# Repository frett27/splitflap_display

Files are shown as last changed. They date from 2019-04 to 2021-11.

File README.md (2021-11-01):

# Split Flap Display

*Patrice Freydiere - Avril/Septembre 2019*

This repository contains the technical elements to create a flip flap display module, This display can be used for a physical web counter, a clock, letter display.

Parametric design permit to use other elements to display (picto, drawing).

### Key Design Concept

The FlipFlap module aim to reduce the number of part to build it. Modules are connected to each others and contribute to display large messages. The module is only responsible to manage the mechanics and contribution intelligence.

Using standard PVC card helps have nice diplay digits, they are easy to setup as there are printers allowing to create the fonts.

Using SCAD as modeler permit to have adaptative design, and change the dimensions.

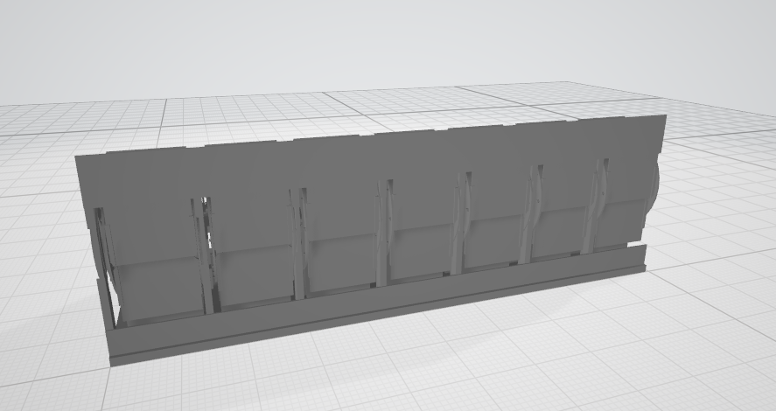
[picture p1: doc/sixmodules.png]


Four Spaces Modules:

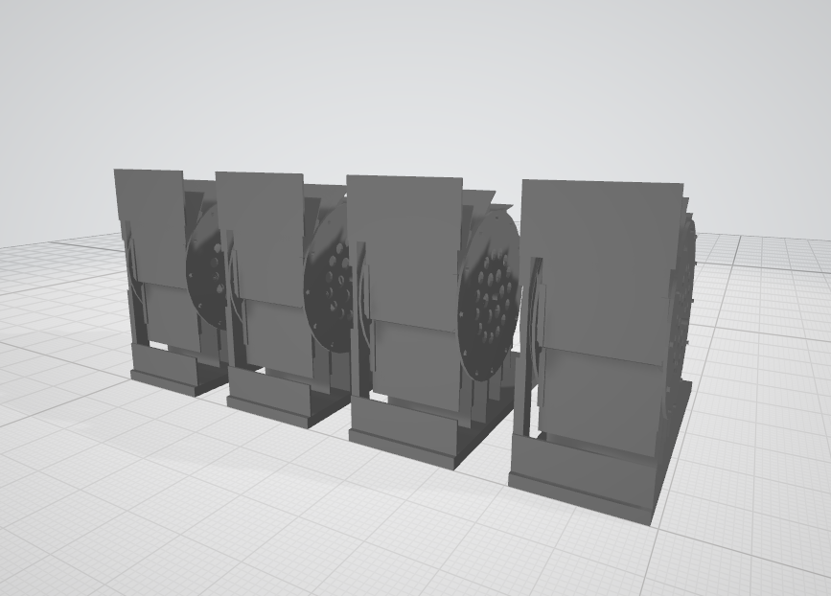
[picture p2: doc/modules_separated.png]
 

Exploded view of one module : (4 main printed parts + cards)

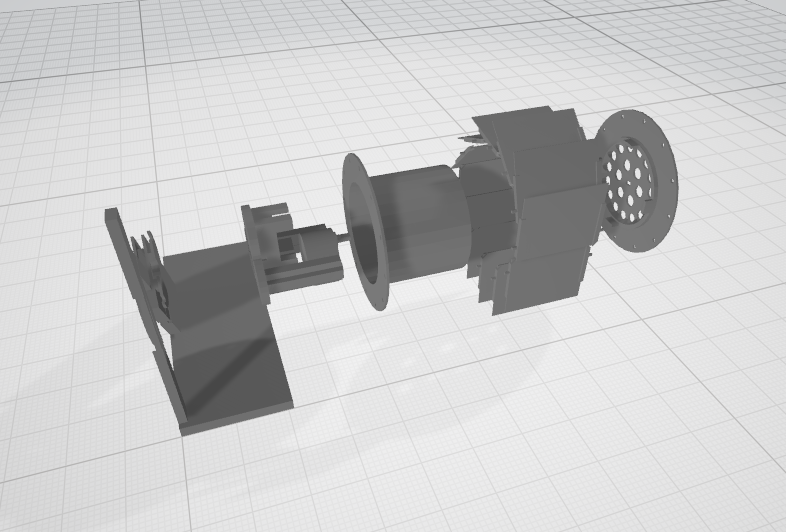
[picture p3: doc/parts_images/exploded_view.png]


This project is used for side projects. All comments, improvements are welcome.

The 3D design aim to be printed, with a minimum parts number. 

for more informations, go to **doc/** folder on how to print and build

# Project State

#### V1

- [x] 3D Print - V1 
- [x] Electronic Schematic
- [x] Card Mounting
- [x] Software
- [x] Structure for fix

#### V2

3D Design

- [x] Thick enlrge for switch
- [x] Redesign card fixtures
- [x] Support Design, to be simple light and permit to add decorations.
- [x] Add switch on electronic Card & Pullup

#### **V2.1**

- [x] Testing the Software Serial, apparently an error in choosing the pins 3 is not interrupted changed compatible ->, use 8 or 9

#### **V3 - New electronic**

integrating the upstream serial and downstream serial, works both.

#### **V4 - Electronic change**

Fix a pin placement issue

## Credits

This project is inspired from  [Dead_simple_split_flap_display_ 's work](https://www.thingiverse.com/thing:2369832)

And [splitflap](https://github.com/scottbez1/splitflap) work (upon the buiding simplification)

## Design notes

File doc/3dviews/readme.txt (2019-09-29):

Stl Viewer v1.07
================

Installation:
-------------
upload those files into your web server:
stl_viewer.min.js 
parser.min.js 
load_stl.min.js 
webgl_detector.js 
CanvasRenderer.js 
OrbitControls.js
TrackballControls.js
Projector.js 
three.min.js

Usage:
------
At the html body:

<script src="stl_viewer.min.js"></script>

<script>
	var stl_viewer=new StlViewer(document.getElementById("stl_cont"), { models: [ {id:0, filename:"mystl.stl"} ] });
</script>

Documentation & License details:
--------------------------------
https://www.viewstl.com/plugin/

by Omri Rips, Viewstl.com

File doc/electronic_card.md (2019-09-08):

# Electronic Card

*Patrice Freydiere - 2019*

The electronic is module specific, but can be connected with others modules to create a variable length number.

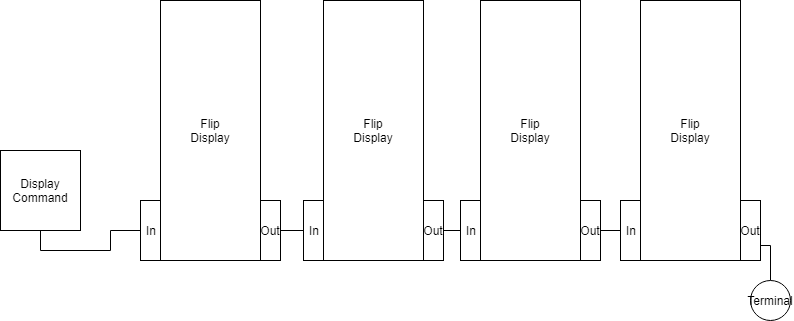
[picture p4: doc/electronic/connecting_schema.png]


Every modules have a in-connector and out-connector. They transmit information upward and backward using a serial communication.

Inside the module, the main controller, is connected to the stepper motor driver, and the out-connector.

Basic schema of the electronic elements associated to modules :

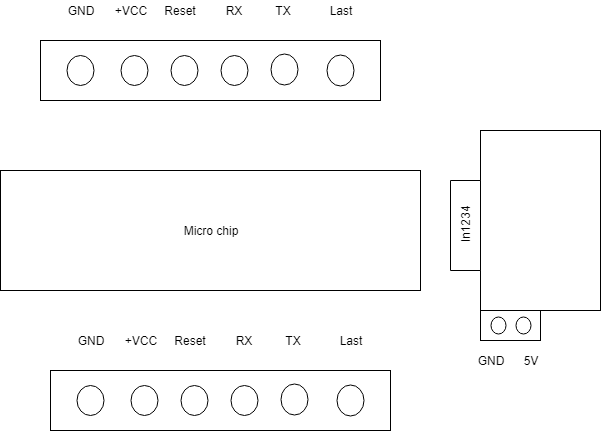
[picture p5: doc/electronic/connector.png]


## Electronic Schema

The schema is as follow :

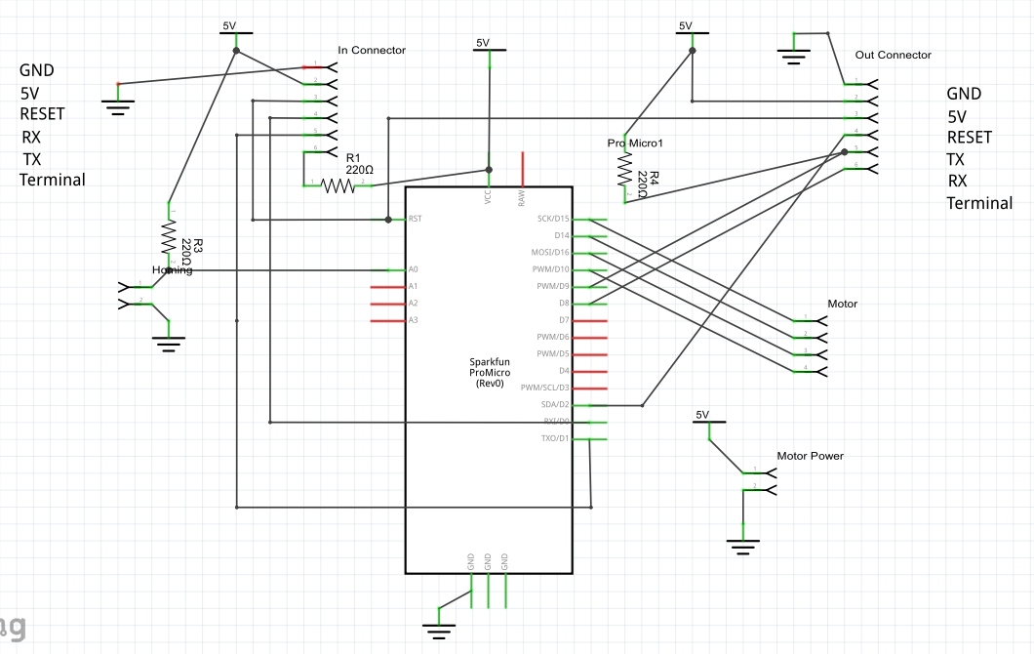
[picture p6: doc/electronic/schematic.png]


### Connector pins

Slot from the input side

<-  on the input side

- GND
- VCC
- RESET
- RX
- TX
- pull up connection

On the other side / symetric

- GND
- VCC
- RESET
- TX
- RX
- Connected

### The electronic software logic:

To have more information about the control of the digit using the serial port, see [](flip_controlling.md)

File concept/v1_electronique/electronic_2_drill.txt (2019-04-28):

; NON-PLATED HOLES START AT T1
; THROUGH (PLATED) HOLES START AT T100
M48
INCH
T1C0.086614
T100C0.035000
T101C0.035433
T102C0.038000
%
T1
X018699Y001581
X001735Y001722
X001524Y012808
X018875Y012914
T100
X010034Y004460
X017034Y010460
X016034Y010460
X014034Y010460
X018034Y004460
X013034Y010460
X008320Y013113
X007034Y010460
X015034Y004460
X010034Y010460
X009034Y004460
X012034Y004460
X008034Y004460
X004320Y013113
X011034Y004460
X018034Y010460
X015034Y010460
X009034Y010460
X017034Y004460
X012034Y010460
X008034Y010460
X016034Y004460
X011034Y010460
X014034Y004460
X013034Y004460
X007034Y004460
T101
X014760Y009341
X019560Y006221
X016680Y008861
X012360Y006221
T102
X014414Y001602
X002343Y010150
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

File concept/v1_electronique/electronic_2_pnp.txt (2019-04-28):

*Pick And Place List
*Company=
*Author=
*eMail=
*
*Project=electronic_2
*Date=22:58:21
*CreatedBy=Fritzing 0.9.2b.11.19.8d2d5970658f0bed09c661c9ea9a515b5f40f44c
*
*
*Coordinates in mm, always center of component
*Origin 0/0=Lower left corner of PCB
*Rotation in degree (0-360, math. pos.)
*
*No;Value;Package;X;Y;Rotation;Side;Name
1;;;37.1785;-30.0187;90;Bottom;TXT3
2;;;9.1479;-25.4851;0;Bottom;TXT3
3;;THT;35.9448;-32.1225;90;Bottom;In Connector
4;;;28.7267;-1.64689;90;Bottom;TXT3
5;;;42.2378;-30.0701;90;Bottom;TXT3
6;;;29.3816;-30.2896;90;Bottom;TXT3
7;;;12.6508;-3.29659;0;Bottom;TXT1
8;;;31.3944;-15.8039;0;Bottom;Via3
9;;;39.7373;-30.2059;90;Bottom;TXT3
10;;;15.7577;-5.1997;0;Bottom;TXT1
11;;THT;5.95336;-24.5128;0;Bottom;Motor
12;;;4.40904;-4.37463;0;Bottom;Hole2
13;;;34.467;-30.3414;90;Bottom;TXT3
14;;THT;5.417;-11.4922;0;Bottom;Motor Power
15;;;47.4965;-4.01706;0;Bottom;Hole1
16;;;3.87269;-32.5335;0;Bottom;Hole4
17;;;47.9435;-32.8016;0;Bottom;Hole3
18;;;7.90221;-13.1062;90;Bottom;TXT3
19;;;9.07006;-28.1321;0;Bottom;TXT3
20;;;49.6824;-15.8039;0;Bottom;Via2
21;;;33.1065;-18.9495;90;Bottom;Pro Micro1
22;;;42.3672;-22.5095;0;Bottom;Via1
23;;;36.5236;-1.37596;90;Bottom;TXT3
24;220;THT;16.053;-33.3083;-180;Bottom;R1
25;;;9.30361;-20.191;0;Bottom;TXT3
26;;;37.4904;-23.7287;0;Bottom;Via4
27;;;7.98007;-9.99205;90;Bottom;TXT3
28;;;41.5829;-1.42741;90;Bottom;TXT3
29;;;31.3608;-1.69869;90;Bottom;TXT3
30;;;39.0824;-1.56322;90;Bottom;TXT3
31;;THT;35.3421;-4.06946;90;Bottom;Out Connector
32;;;34.1153;-1.56322;90;Bottom;TXT3
33;;;9.18683;-22.877;0;Bottom;TXT3
34;;;32.0609;-30.464;90;Bottom;TXT3

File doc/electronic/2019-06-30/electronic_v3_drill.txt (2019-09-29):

; NON-PLATED HOLES START AT T1
; THROUGH (PLATED) HOLES START AT T100
M48
INCH
T1C0.086614
T100C0.035000
T101C0.035433
T102C0.038000
%
T1
X018685Y017217
X001461Y017174
X001672Y001500
X018541Y001486
T100
X017910Y012301
X014910Y012301
X013910Y012301
X008910Y012301
X016910Y006301
X011910Y012301
X010060Y014917
X007910Y012301
X015910Y006301
X006060Y014917
X010910Y012301
X009910Y006301
X012910Y006301
X010181Y010503
X006910Y006301
X016910Y012301
X015910Y012301
X009910Y012301
X017910Y006301
X017126Y008793
X012910Y012301
X006910Y012301
X014910Y006301
X013910Y006301
X013126Y008793
X008910Y006301
X006181Y010503
X011910Y006301
X007910Y006301
X010910Y006301
T101
X006840Y017485
X007080Y016285
T102
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

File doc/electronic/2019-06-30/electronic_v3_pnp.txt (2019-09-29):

*Pick And Place List
*Company=
*Author=
*eMail=
*
*Project=electronic_v3
*Date=16:30:38
*CreatedBy=Fritzing 0.9.2b.11.19.8d2d5970658f0bed09c661c9ea9a515b5f40f44c
*
*
*Coordinates in mm, always center of component
*Origin 0/0=Lower left corner of PCB
*Rotation in degree (0-360, math. pos.)
*
*No;Value;Package;X;Y;Rotation;Side;Name
1;;;36.363;-2.74234;90;Bottom;TXT3
2;220;THT;20.7815;-26.6781;0;Bottom;R4
3;;THT;35.7038;-42.731;90;Bottom;In Connector
4;;THT;35.2619;-5.83768;90;Bottom;Out Connector
5;;;31.2002;-3.06507;90;Bottom;TXT3
6;;;8.02289;-33.0397;0;Bottom;TXT3
7;;;8.06181;-30.4316;0;Bottom;TXT3
8;;;31.8199;-41.0725;90;Bottom;TXT3
9;;;17.9832;-41.3643;0;Bottom;Via2
10;;;41.4223;-2.79379;90;Bottom;TXT3
11;;;47.0948;-3.77611;0;Bottom;Hole1
12;;;41.9968;-40.6787;90;Bottom;TXT3
13;;;34.226;-40.9499;90;Bottom;TXT3
14;;THT;11.3984;-42.7993;90;Bottom;Homing
15;;;25.7204;-10.8755;0;Bottom;TXT1
16;;;17.3736;-44.4123;0;Bottom;Via1
17;;;3.71208;-43.6241;0;Bottom;Hole4
18;;;33.9547;-2.92961;90;Bottom;TXT3
19;;THT;3.80977;-12.2156;0;Bottom;Motor Power
20;;;28.5661;-3.01327;90;Bottom;TXT3
21;;;29.1406;-40.8981;90;Bottom;TXT3
22;;;47.4614;-43.7316;0;Bottom;Hole3
23;;;7.49799;-14.8946;90;Bottom;TXT3
24;220;THT;38.4222;-22.3355;180;Bottom;R3
25;;;36.9375;-40.6272;90;Bottom;TXT3
26;;;4.24845;-3.81223;0;Bottom;Hole2
27;;;39.4963;-40.8145;90;Bottom;TXT3
28;;;32.7933;-23.6268;90;Bottom;Pro Micro1
29;;;38.9218;-2.92961;90;Bottom;TXT3
30;;;8.17859;-27.7456;0;Bottom;TXT3
31;;;7.42012;-18.0088;90;Bottom;TXT3
32;;;14.5797;-1.36796;0;Bottom;TXT1
33;;;7.94503;-35.6868;0;Bottom;TXT3
34;;THT;3.94431;-31.8263;0;Bottom;Motor
35;220;THT;20.4732;-37.8894;180;Bottom;R1

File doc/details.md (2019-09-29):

# A more detailed insight about Split flap display module

The FlipFlap module aim to reduce the number of part to build it.  4 printed parts are needed to build one. 



a PCB manage motors and serial communication on both usage : standalone, or serial.

Modules does not include the front panel. this permit to change color, boxing.



Four Modules:

 

Exploded view of one module : (4 main printed parts + cards)

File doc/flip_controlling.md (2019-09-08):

# Flip controlling - Protocol

*Patrice Freydiere - 2019*

### Introduction

This document describe the flip display protocol. It implements a minimum protocol, with an integrated message control, using the length.

The module has two Serial Port for communication : In and Out. And one serial port for command.

Digits module elect the master at the top left of the chain, every digits modules are connected in a serial manner.

### Message protocol

To remain simple, easy to analyze and DEBUG, all messages are in text format.

All Internal messages are sent using the following envelope structure :

"S" + [SIZE_3DIGITS] + [MSG] + [10]

if the message has 10 characters, it is escaped using the "\\" character. 

## Chain control

At init, the module wants to know if he is the latest one, to determine it's number in the stack.

Protocol to initialize the module: send IAM-[] message, the message will be serially forwarded with an updated address. This permit the chain to allocate their addressID. 

By default the initialized id is -1 for each module

| Sequence | Message | Message Orientation | Description | Note |
| --- | --- | --- | --- | ---- |
| 2 | IAM-[NoATTRIBUTED] | [->] MODULE [->] | Define the address for the module. The message is forwarded to the next one, with the next NoAttributed. | |
| 4 | CMD-[NoAttributed]-[MessageLength]-[Command] | [->] MODULE | This command permit to send a specific message to a digit module | |
| 1 | DISPLAY-[MESSAGE] | [->] MODULE [->] | Ask to display the message, the module take the [No] digit number. Each Digits are on 2 digits | |
| 2 | ACKDISPLAY-[NoAttributed] | [<-] MODULE | Acknowledge about the message | |

## Module Display Command

| ID | Message | Message Orientation | Description | Note |
| ---- | --- | --- | --- | --- |
| 3 | DIGIT-[DIGITNO] | [->] MODULE | Ask to display the given digit | Display the digit  number (from 0-12). no ack for this operation |
| 4 | OFFSET | [->] MODULE | Define the homing offset to tune the position of the first flip | |

## Module Stepper Command (Testing)

| ID | Message | Message Orientation | Description | Note |
| ---- | --- | --- | --- | ---- |
| 1 | MOVE-[step] | [->] MODULE | move the digit module to the given step | |

## Module HeartBeat

| ID | Message | Message Orientation | Description | Note |
| ---- | --- | --- | --- | ---- |
| 1 | HELLO | [->] MODULE [->] | Preceding module inform of its status, following module responde HELLO Message also | |

## Error Handling

In case states are not properly covered, some error messages can be sent.

| ID | Message | Message Orientation | Description | Note |
| ---- | --- | --- | --- | ---- |
| 1 | ERROR-[MESSAGE] | [<-] MODULE [<-] | inform of an error | |

## Debug Message

In debugging status, messages can be send, they are not handled by up and down

| ID | Message | Message Orientation | Description | Note |
| ---- | --- | --- | --- | ---- |
| 1 | DEBUG-[MESSAGE] | [->] MODULE [<-] | debug message sent | |

## Message examples

**Hello Message**

```
S005HELLO
```

Response on command Port:

```
Command from Front Executed :HELLO
front send message:S005HELLO
```

**Print a specific DIGIT**

```
S008DIGIT-02
```

Response on command port

```
Command from Front Executed :DIGIT-02
```

**Move stepper to a specific step**

```
S008MOVE-003
```

Response:

```
Command from Front Executed :MOVE-500
```

**Define the offset of the stepper initial offset**

```
S011OFFSET-0500
```

response:

```

Command from Front Executed :OFFSET-0500

```

## Chain Command Examples

to initiate the hole chain, you have to call the IAM function that define the addresses of all connected modules

**Define the chain addresses of modules**

```
S005IAM-0
```

```
Command from Front Executed :IAM-0
back send message:S005IAM-1
```

**Send a specific command to a module in the chain**

```
S016CMD-001-DIGIT-08
```

```
Command from Front Executed :CMD-001-DIGIT-08
Command from Front Executed :DIGIT-08
1750 / 4096
```

**Send a hole display message to the chain**

```
S013DISPLAY-06234
```

Response

```
command from Front Executed :DISPLAY-06234
front send message:S012ACKDISPLAY-1
```

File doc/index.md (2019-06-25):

# Flip Flap - Digit - module (FLIP-1)

*Patrice Freydiere - 2019-04*

This module display a digit, using an energy minimum approach. 



## Feature

- Affordable

- easy to create and mount
- Adaptative

## Dimensions

The module has the following dimensions currently, using a PVC card as reference for the digits.

 "depth=", 109.55, "width=", 59.98, "height=", 152.2

## Components

| Reference | Qty  | Description | Cost Home Made (€) | Cost Parts |
| --- | ---- | --- | --- | --- |
| FLIP-1-3D1 | 1 | Stator | 2 | 5€ / per 20 parts  |
| FLIP-1-3D2 | 1 | Rotor - 1 | 2 | 5€ / per 20 parts  |
| FLIP-1-3D3 | 1 | Rotor - 2 | 2 | 5€ / per 20 parts  |
| FLIP-1-3D4 | 1 | Support for sustain the display | 3 | 10€ / per 20 parts |
| FLIP-1-CARDS | 6 | Flip cards (6 * 2) half cards | 30€ per 500 pieces | |
| FLIP-1-MOTOR_CMD | 1 | 28byj-48 - module with command card (LN218) | 4 € each | |
| FLIP-1-SWITCH | 1 | Homing switch | 2 € each | |

<u>Currently in tests:</u>

Vinyl letters :

<https://www.amazon.com/dp/B079HJRG1X/ref=sspa_dk_detail_0?pd_rd_i=B077KDX4NR&th=1>

(2inch)

## 3D model

Model is build with OpenScad, permitting to create parametric models, this is really usefull for optimization and alternatives.

There are 4 parts, 



The support :

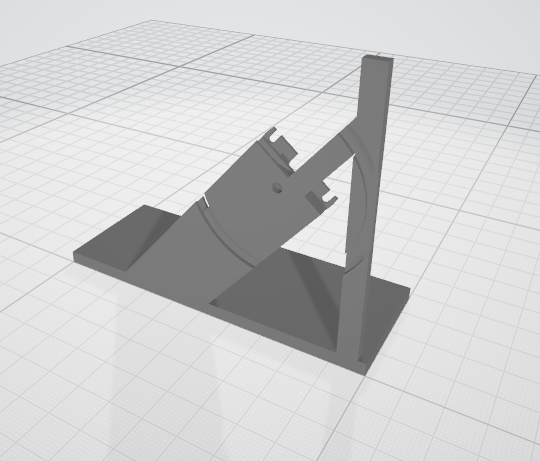
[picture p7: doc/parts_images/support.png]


The rotor in 2 parts, 

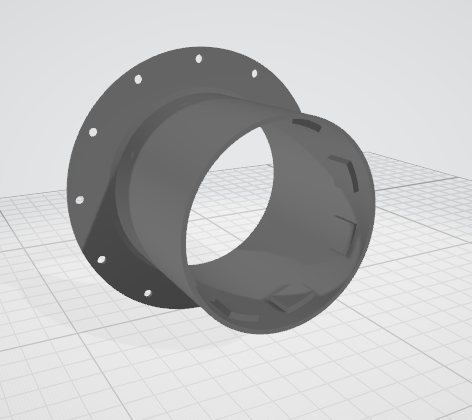
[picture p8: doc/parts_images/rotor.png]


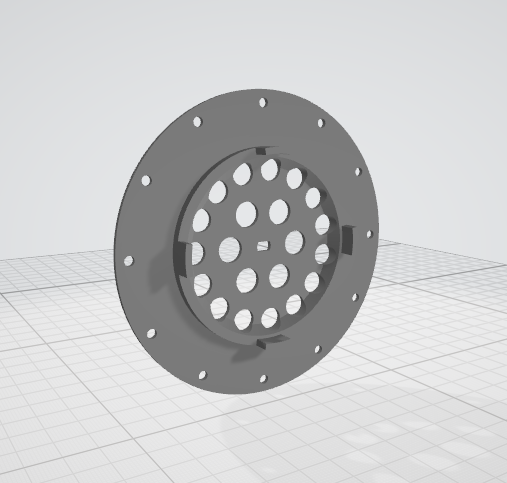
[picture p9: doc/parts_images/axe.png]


And the stator for the mounting elements :

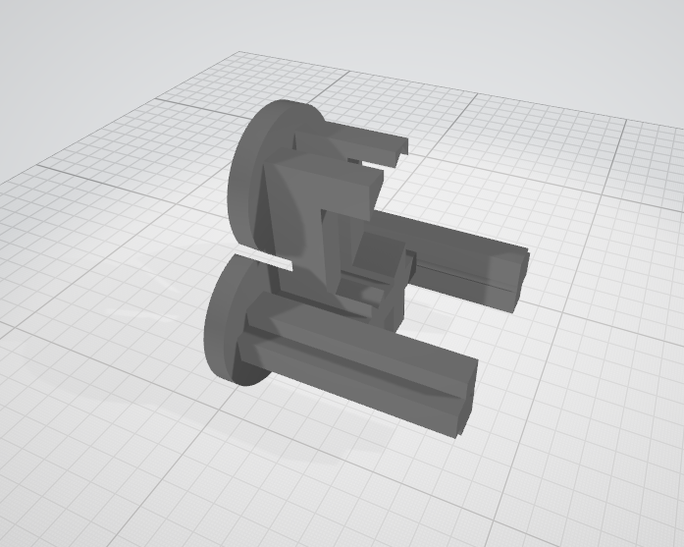
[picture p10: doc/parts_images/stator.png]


And for card fix :

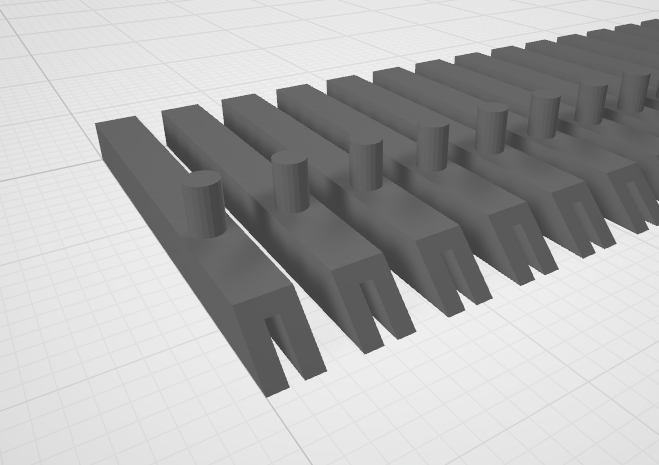
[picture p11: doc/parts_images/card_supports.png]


## Electronic

Electronic card is composed of a leonardo microchip, this chip handle the motor, homing, and communication. And external USB connected unit gives the numbers to display.

A lonely electronic card is hosted in the display.

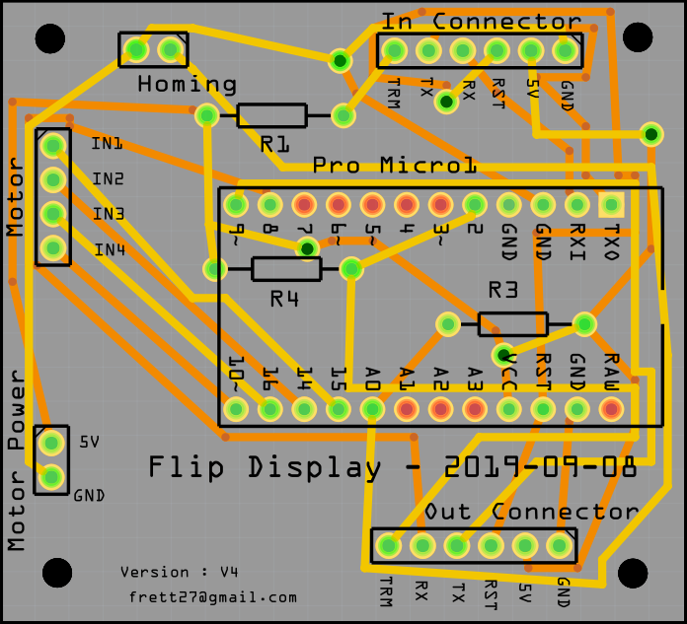
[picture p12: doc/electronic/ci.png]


## How to mount flip display

Step 1 : solder the switch, 

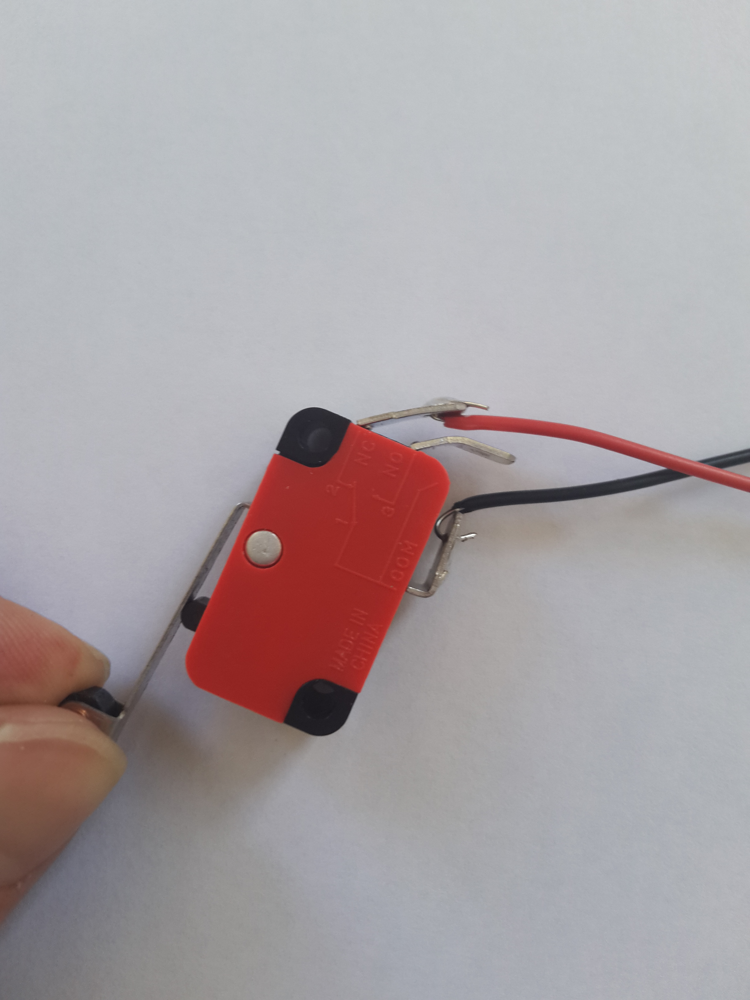
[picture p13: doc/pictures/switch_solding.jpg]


Mount motor on stator :

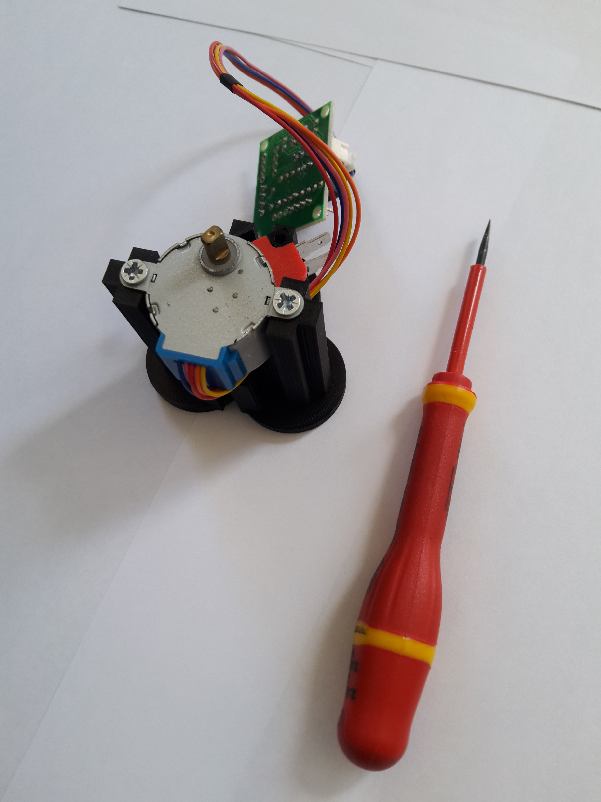
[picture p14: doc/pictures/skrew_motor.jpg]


Switch soldering

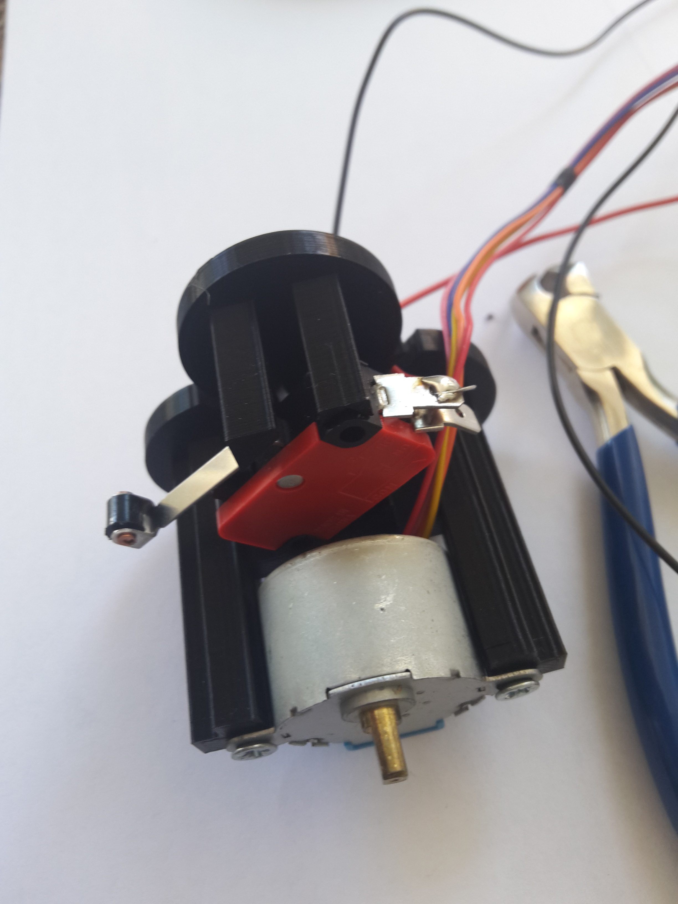
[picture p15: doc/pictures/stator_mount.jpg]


Put the stator into the mounted rotor and fix them on the support using the 2 skrews. Take caution of the cable there is calculated space to not make the cable be damaged.

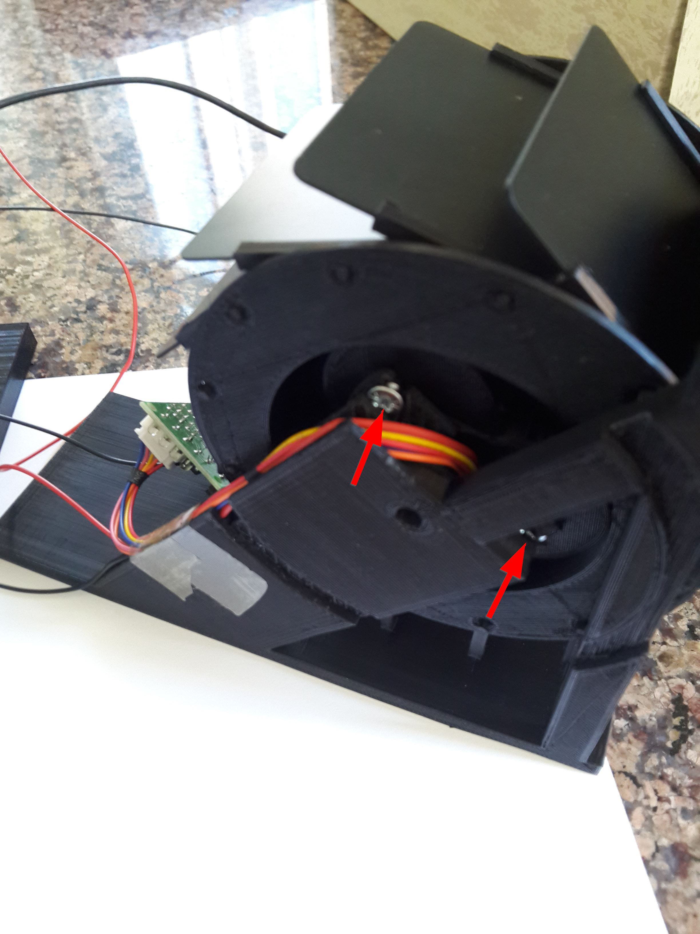
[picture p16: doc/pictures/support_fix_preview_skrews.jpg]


The mounted result :

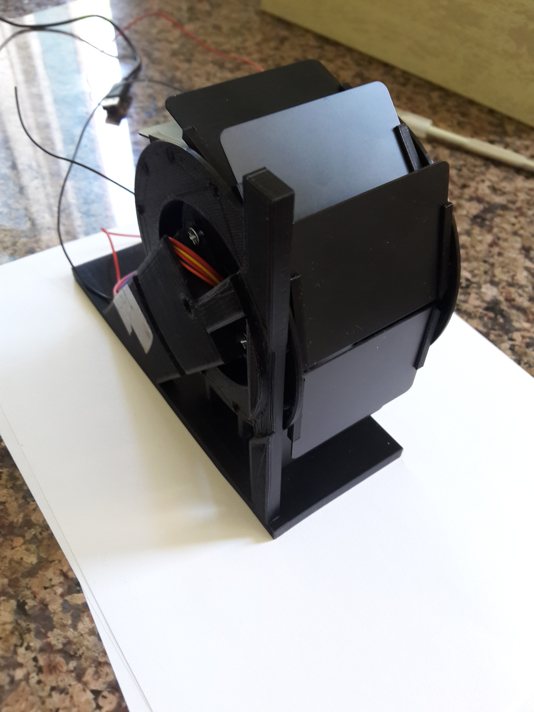
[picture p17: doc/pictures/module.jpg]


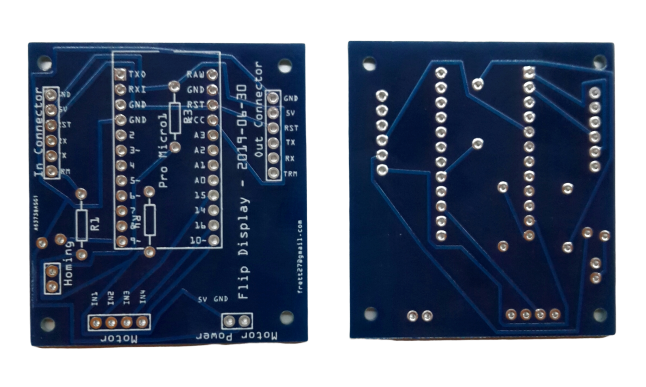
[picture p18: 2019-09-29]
doc/electronic/cards_v3-nobg.png

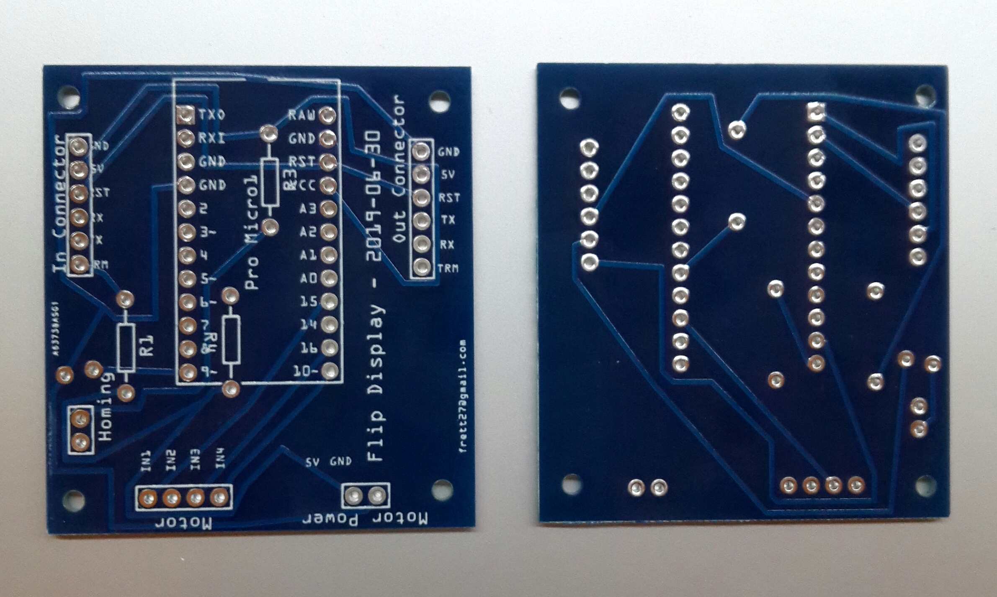
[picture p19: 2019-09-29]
doc/electronic/cards_v3.jpg

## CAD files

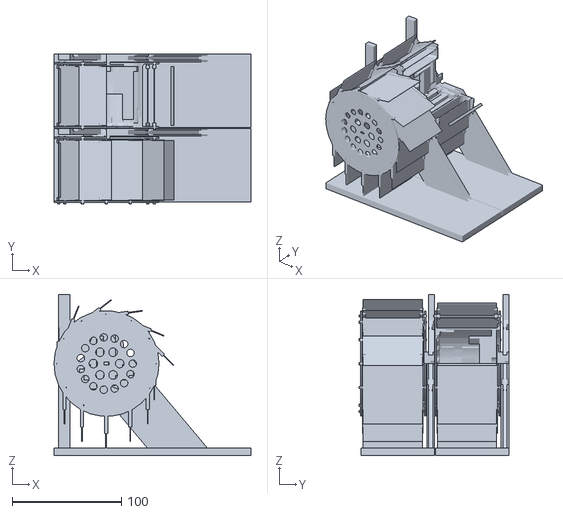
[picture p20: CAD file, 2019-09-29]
doc/3dviews/view_2_modules_with_cut.stl
180.0 x 136.8 x 147.3

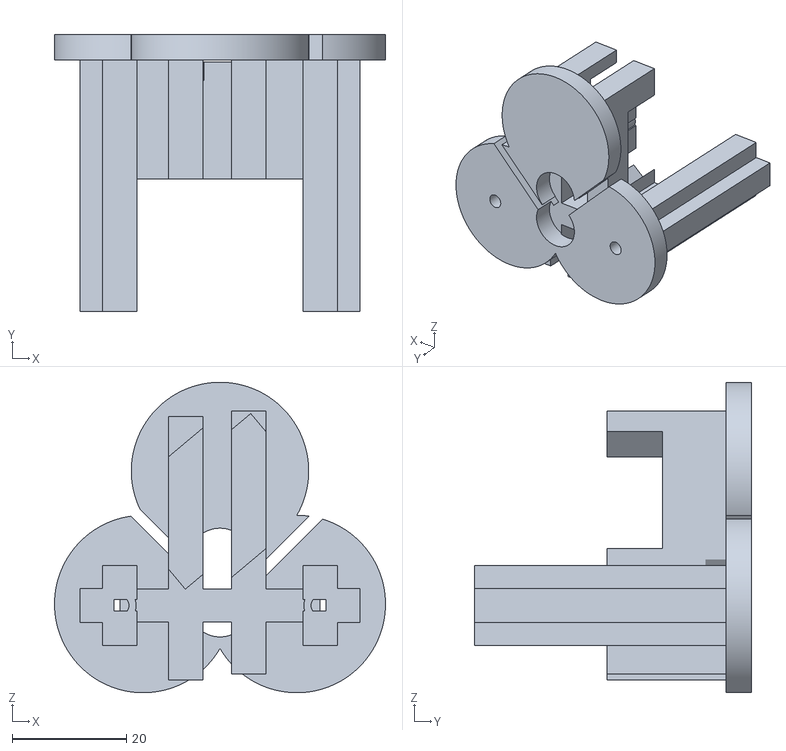
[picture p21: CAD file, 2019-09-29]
stl/stator.stl
57.8 x 48.5 x 54.3

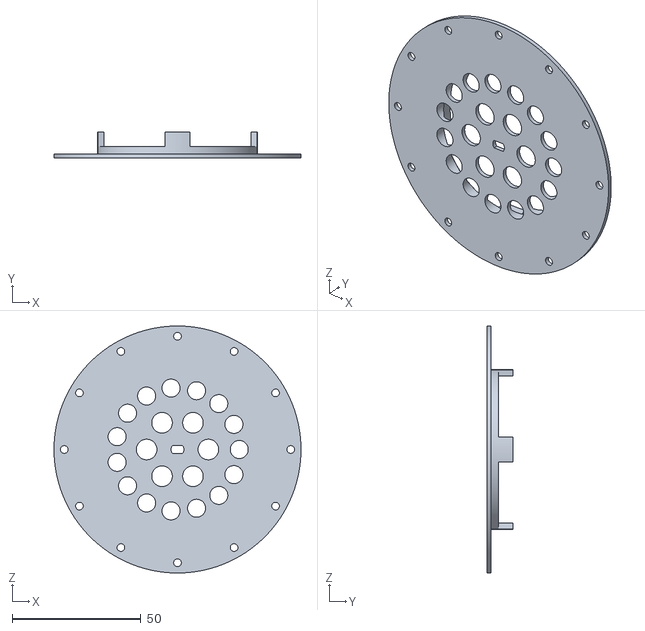
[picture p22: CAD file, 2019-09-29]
stl/axe.stl
96.0 x 10.0 x 96.0

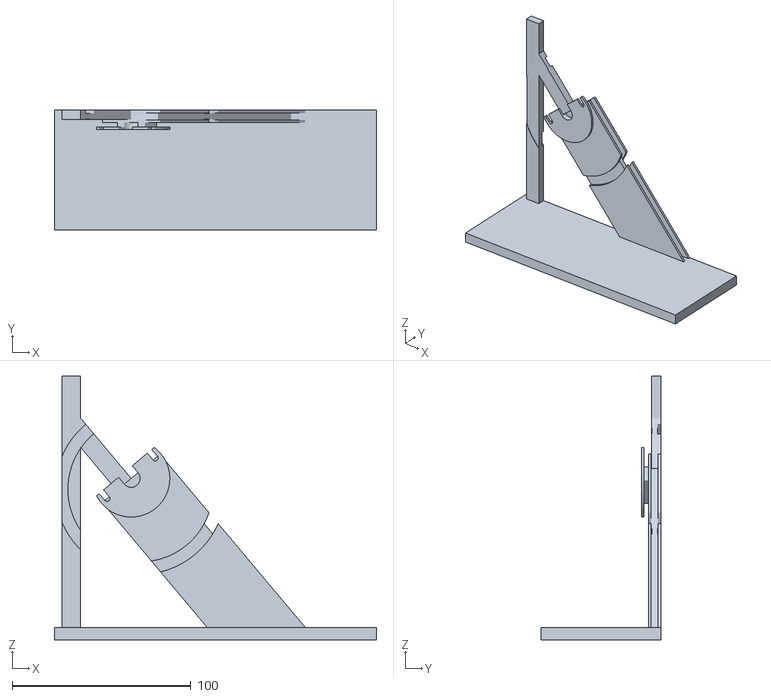
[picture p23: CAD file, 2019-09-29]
stl/support.stl
180.0 x 67.0 x 147.3

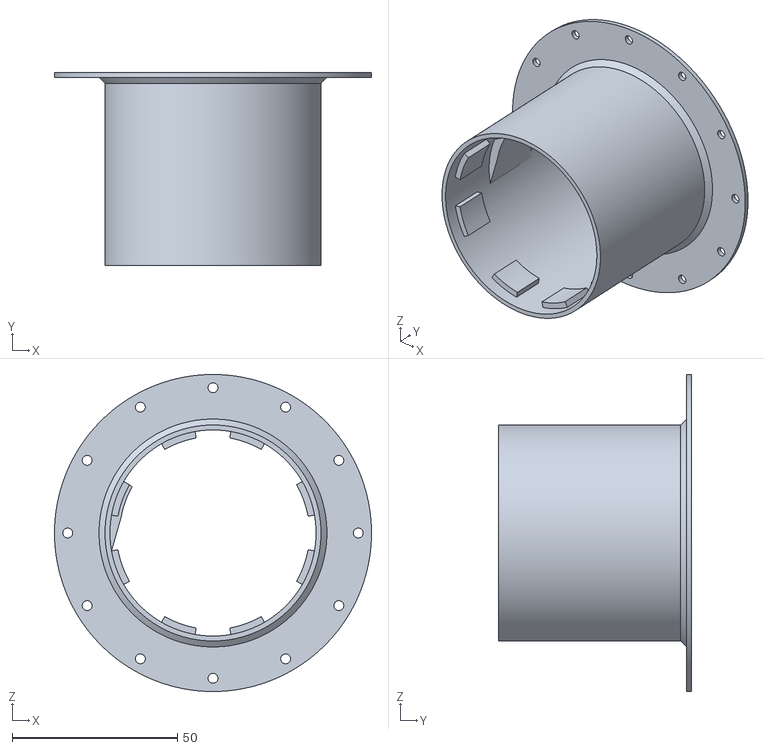
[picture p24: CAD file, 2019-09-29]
stl/rotor.stl
96.0 x 58.4 x 96.0

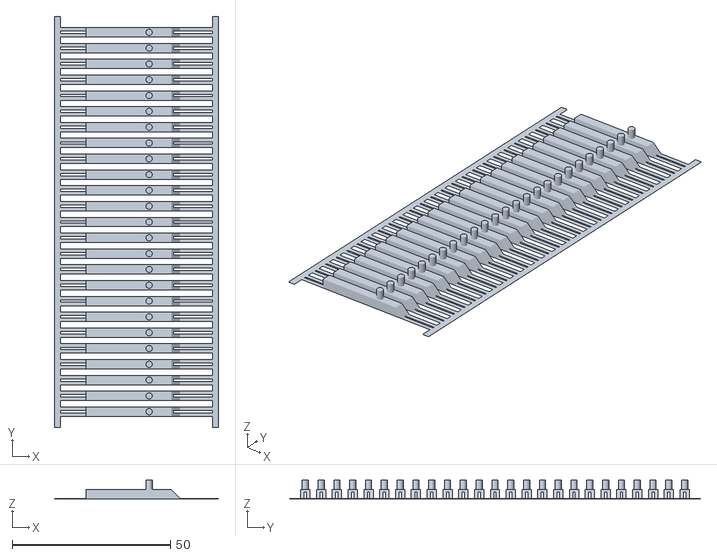
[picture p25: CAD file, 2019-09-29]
stl/fixations.stl
52.0 x 130.0 x 6.00

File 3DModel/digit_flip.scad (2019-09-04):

include <relativity.scad>
include <28byj-48.scad>
include <switch.scad>

////////////////////////////////////////////////////////////
//
//  Parameters for the design
//
////////////////////////////////////////////////////////////

// pvc card dimensions

pvc_card_width = 53.98;

// card support thick
support_flip_thick = 0.75;

flip_width = pvc_card_width + 2*support_flip_thick;
flip_height = 86.2/2; //2
flip_thick = 0.75;

flips_numbers = 12;
thick = 1.5;

// fixture size
flip_fixure_diameter = 2;

// play for the flip fixture, for rotating
flip_fixure_diameter_play = 1; // in diameter

// radius for flip rotating fix

/* initialement 42 */
radius_flip_position = 44; 
// flip axis distance
/* initialement 7.5 */
deport = 10;

// distance between the flip holes and external
margin_axe_external = 4;

// motor distance link
max_internal_radius = 42 /* radius_flip_position */ - 11;

// play for letting the elements move
// 0.2 is good
play = 0.2;
transverse_play = play + 0.5;


/////////////////////////////////
// internal generation parameters

angle_flip = 360/flips_numbers;
axe_external_diameter = 
                (radius_flip_position +
                 margin_axe_external) * 2;

// internal centring
internal_centring_elements_height = 2;

fixing_height = 28byj48_chassis_height + (flip_width - 28byj48_chassis_height) - 28byj48_shaft_height + 28byj48_shaft_slotted_height / 2;

// general animation angle parameters
general_rotation_angle = 0;

// drawing generation precision
// uncomment this for generating STL,
//

 $fa = 1;
 $fs=0.3;


module flip(width=flip_width) {
    // flip_fixure_diameter/2
    translate([0,0,0]) {
        
        translate([0,deport,0]) { // deport
            box(size=[width - 2 * support_flip_thick,
                        flip_height,
                        flip_thick],
                anchor=[0,1,1]);
        }


        // 1 
        translate([-width/2+support_flip_thick,0,0])
        rotate([0,180,0]) // flip to have the pin on proper direction
       
        rotate([0,0,90]) // orient along card
        translate([0,0, flip_thick / 2])
        support_flip_card_reference();
        
        translate([width/2 - support_flip_thick,0,0])
        
        rotate([0,0,90]) // orient along card
        translate([0,0, - flip_thick / 2])
        support_flip_card_reference();
                
    }
}


module axe() {
    
     rotate([0,general_rotation_angle,0]) {
            translated(thick/2 * y)
            orient([y])
            differed("hole")
            
            rod(d=axe_external_diameter ,h=thick)
            
            for (i = [0: flips_numbers]) {
                orient([z])
                rotated(angle_flip*i*z)
                translated(radius_flip_position  *x)
                rod(d=flip_fixure_diameter 
                       + flip_fixure_diameter_play,h=10, $class="hole");
            }
        };
}

module axe_with_holes() {
  
    difference() {
       
        union(){
            
          rotate([-90,0,0])
          rotate_extrude(convexity = 10)
          polygon(points = [
            [ (max_internal_radius) ,
               0],
            [  (max_internal_radius) ,
               3 * thick],
            [  (max_internal_radius - 2 * thick) ,
               3 * thick],
            
            [(max_internal_radius - 5 * thick) ,
               0]
          ]);
          axe();
            
          // pattes   
          
          for(i = [0:3]) {
              internal_radius = max_internal_radius;
              element_width = 10;
            
              rotated([0,90 * i,0])
              translate([0,element_width/2,-internal_radius])
              rotate([90,0,0])
              arc(rayon=internal_radius,
                  height=internal_centring_elements_height,
                  width=element_width, 
                  angle_start=-9, 
                  angle_end=9);

          }
            
          // axis tube
          
          rotate([90,0,0])
          translate([0,0,-thick])
          cylinder(d = 28byj48_shaft_radius * 3, h = thick);
            
        };
        
        // holes
        union() {
            
                // internal
                nb_internal = 6;
                for( i = [0:nb_internal]) {
                    rotate([0,i * 360/nb_internal +
                    general_rotation_angle,0])                    translate([12,10*thick,0]) 
                    rotate([90,0,0]) 
                    cylinder(d=8,h=20*thick);
                };
            
                for( i = [0:15]) {
                    rotate([0,i * 360/15 +
                        general_rotation_angle,0])                    translate([24,10*thick,0])
                    rotate([90,0,0])
                    cylinder(d=7,h=20*thick);
                };
        }
    }
    
   
    

}

// function to place flips with angle and index
module place_flip(index = 0, relative_angle = 0) {
     // second flip
    rotate([0, - index * angle_flip + general_rotation_angle ,0]) {
        translate([radius_flip_position,flip_width/2,0]) {
            rotate([0,
                    -90 + relative_angle 
                        - general_rotation_angle,
                    0]) {
                rotate([0,0,90]) {
           
                flip(width= flip_width);
             }
            }
        }
    }
}


// place the flips around the 12 holes design
module montage() {
    
    // one flip
    
    place_flip(0, relative_angle = 180);
    place_flip(1, relative_angle=180 - 15);
    place_flip(2, relative_angle=180 - 8);
    place_flip(3, relative_angle=180 - 8);
    place_flip(4, relative_angle=180 - 8);
    place_flip(5, relative_angle=180 - 8);
    place_flip(6, relative_angle=180 - 0);
    place_flip(7, relative_angle=angle_flip);
    
    place_flip(8, relative_angle=2 * angle_flip);
   
    place_flip(9, relative_angle=3 * angle_flip);

    place_flip(10, relative_angle=4 * angle_flip);

    place_flip(11, relative_angle=5 * angle_flip);
   
}

/*
// place the butee for the flip
module butee() {
    butee_width = flip_width + 2 * thick;
    translated( (flip_width * z) + 
            ( radius_flip_position + thick) * x - 
            2 * thick * z 
               )
    box(size = [2,butee_width,5],anchor=[-1,-1,-1]);
}
*/

// show motor
module motor() {
    differed("bords") {
        
        rod(d = 20, h = 25,anchor=[0,0,1])
        align([0,0,1]) {
            rod(d = 2, h=8.1);
        
            translated((20/2 + 15.1/2) * x + -30 * z) 
            box(size=[20, 30, 30], $class="bords");

            rotated(180*z)
            translated((20/2 + 15.1/2) * x + -30 * z) 
            box(size=[20, 30, 30], $class="bords");
        }
    };
}

// utility tube module
module tube(d,h,perfo) {
    differed("trou","plein") {
     rod(d=d, h=h, $class="plein",anchor= [0,0,-1] );
     translate( [0,0,-1]) rod(d=perfo,h=h+2, anchor= [0,0,-1] , $class="trou");
 }
}


module threecircles(diameter=20, flips_numbers=5, height=thick) {
    
    rod(d=diameter, h=height);
    for(i = [0:360/flips_numbers:360]) {
        rotated([0,0,i])
        translated(diameter/2 * x)
        rod(d=diameter, h=height);    
    }
}

skrew_hole_size = 28byj48_mount_hole_radius * 2-1;
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

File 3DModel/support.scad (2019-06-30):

// use <libraries/paratslot_for_openscad_201205/paratslot.scad>

include <digit_flip.scad>;


// distance from axis to base
structure_height = (flip_height - deport + radius_flip_position);

// echo (structure_height);

bottom_support_height = 7;

sustain_structure_thick = 7;


angle_pylon = 40;

height_axis = 2*28byj48_shaft_offset;

main_structure_height = (structure_height * 2)/cos(angle_pylon);


diameter_flip= 2 * radius_flip_position;




//$fa = 1;
//$fs=0.3;


////////////////////////////////////////////////////
//

module _support_pylon_real() {
    translate([-2 * sustain_structure_thick,0,0])
    for (i = [0:2]) {
        translate([i*14,0,0])
        translate([0,3.5,-main_structure_height/2])
        twotslot(h=structure_height,w=sustain_structure_thick);
    }
}

module _support_pylon() {
    
    pylon_width = 42;
    
    difference() { // for hole for the next axis
        
        union() {
            difference() {
               box(size=[pylon_width,sustain_structure_thick,      
                         main_structure_height],
                         anchor=[0,-1,1]);
            
               // cable pass
               depth = 6;
               mirror([1,0,0])
               union() {
                   // on the pylon side
                   translate([-pylon_width/2,
                                thick])
                   box(size= [depth, sustain_structure_thick - 2 * thick, 
                              main_structure_height],
                        anchor=[-1,-1,1]);
                   
                   // on the top to help guide the cables
                   rotate([0,-angle_pylon/2,0])// angle for passing cables
                   translate([0,thick,0])
                   box(size= [pylon_width, 
                          sustain_structure_thick - 2 * thick,
                          depth],
                        anchor=[0,-1,-1]);
                   
                   
               }
            }
            
            // upper support
            upper_pylon_width = sustain_structure_thick * 3 / 4;
            translate([0,
                       sustain_structure_thick - upper_pylon_width]) {
                d = pylon_width/4;
                
                
                    box(size=[d,
                              upper_pylon_width,
                              radius_flip_position ],
                        anchor=[1,-1,-1]);
                
                translate([0,0, radius_flip_position])
                rotate([0,angle_pylon,0])
                box(size=[d,
                          upper_pylon_width,
                          (flip_height - deport)*sin(45)], // angle
                    anchor=[1,-1,-1]);
                    
                translate([0,0, radius_flip_position])
                rotate([0,angle_pylon,0])
                box(size=[d,
                          upper_pylon_width,
                          main_structure_height],
                    anchor=[1,-1,1]);
                
            }
        }
        
            // hole for passing the next module axis
         hole_diameter = 28byj48_shaft_radius * 2 + play;
         translated(- 28byj48_shaft_offset*z 
                    + (sustain_structure_thick ) *y) 
                // for having the hole at 0
         orient(y)
         rod(d=hole_diameter, 
             h=sustain_structure_thick , 
             anchor=[0,0,0]);
    }
}

// _support_pylon();

top_distance = radius_flip_position + (flip_height - deport)*sin(45);
distance_to_support = 4; // mm from holes


// distance_to_support = 6; // mm from holes

module oblong(width=10, height=30, thick=2, class="oblong") {
    rod(d=width,h=thick, $class=class)
    box(size=[width,height,thick],anchor=[0,1,0], $class=class);
}


module _support_fixation_stator() {
        orient([0,1,0])
        differed("hole") {
                
                rod(h=thick, 
                d= 2 * 28byj48_mount_center_offset 
                    + skrew_hole_size +5 ,
                anchor =[0,0,-1])
                align([0,0,1])
                translated(5*y)
                box(size=[20,
                          10,
                          distance_to_support - thick],
                    anchor=[0,0,-1])
               
                 
                translated(-10*y)
                box(size=[50,50,50],$class="hole", 
                            anchor=[0,1,0]);
            
                // central    
                oblong(thick=90, 
                       width=10, 
                       class="hole");
                
                // trous        
                translated((height_axis + skrew_hole_size / 2)*x)
                oblong(width=skrew_hole_size,thick=90 , class="hole");
                translated(-(height_axis + skrew_hole_size /2)*x)
                
                
                oblong(width=skrew_hole_size,thick=90 , class="hole");
                
                
        }

}
// offset_part = 55;

// distance from center motor axis and the fixing
// plane
offset_part = 56.5;


module ground() {
    translated(- (structure_height + bottom_support_height) * z)
    box(size=[500,500,500],anchor=[0,0,1]);
}

module support() {
    rotated( -angle_pylon *y)
    translated(offset_part * y) {
        
        difference() {    
            translated(28byj48_shaft_offset*z)
            {
                _support_fixation_stator();
                
                translated(distance_to_support*y)
                
                _support_pylon();

                
            };
            
            // pin way
            union() {
                margin = 7;
                way_height = 2;
                
                // 1st way
                translated(distance_to_support*y - 0.01 * y)
                rotate([-90,0,0])
                tube(d=diameter_flip + margin,
                       perfo=diameter_flip - margin,
                       h=way_height);
                
                // 2nd way
                translated( (distance_to_support 
                             + sustain_structure_thick 
                            - way_height) * y)
                rotate([-90,0,0])
                tube(d=diameter_flip + margin,
                       perfo=diameter_flip - margin,
                       h=way_height + 0.1);
                
            }
        }
    }
    
    dalle_g();
}

// support();

base_support_width = 180;

module front_panels() {
    
     // bottom
     translated((offset_part 
                + distance_to_support 
                + sustain_structure_thick) * y
                -structure_height *z +
    
               -(base_support_width / 2 
                    - axe_external_diameter / 2 + thick) * x
               )
     box(size = [thick,base_support_large, 20 ], 
         anchor=[1,1,-1] );

     // up
     translated((offset_part 
                + distance_to_support 
                + sustain_structure_thick) * y
                + top_distance *z +
    
               -(base_support_width / 2 
                    - axe_external_diameter / 2 + thick) * x
               )
     box(size = [thick,base_support_large, 35 ], 
         anchor=[1,1,1] );


}

// support();

//front_panels();

base_support_large = 60 + sustain_structure_thick;

module dalle_g() {
   
    translated((offset_part 
                + distance_to_support 
                + sustain_structure_thick) * y
                -structure_height *z +
               (base_support_width / 2 - axe_external_diameter / 2) * x
               )
   dalle(); 
    
}

module dalle() {
    // dalle
    
    box(size=[base_support_width, base_support_large ,          bottom_support_height], 
        anchor=[0,1,1]);
    
}


///////////////////////////////////////////////////////////
// Assembly


module display_modules(number_of_modules = 6, margin = 2) {

    multiple_shift_position = base_support_large;
    for( i = [0:number_of_modules]) {
        
        translate([0, -(multiple_shift_position + margin) * i,0]) {
                
            difference() {
             support();
             ground();
            }
            
            axe_with_fix();
            montage_g();
            rotor_g();
            stator_g();
            front_panels();
            
        }
    }

}

/*
rotate([-90,0,0]) {
display_modules();
}
*/

module global_support() {
    difference() {
             support();
             ground();
            }
}


module cut_view() {

    difference() {
        
        display_modules(number_of_modules = 1, margin = 1);
        // cut to check
        translate([0,-10,0])
        cube(size=[1000,1000,1000]);
    }
}

/*
 // best view with stl viewer
rotate([-90,0,0])
cut_view();
*/


module exploded_view() {

    global_support()

    translate([0,-50,0])
    stator_motor_g();

    translate([0,-120,0])
    rotor_g();

    translate([0,-200,0])
    montage_g();
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

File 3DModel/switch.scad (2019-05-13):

include <relativity.scad>


inter_axes = 24.45;
switch_angle0 = atan(9.41/inter_axes);
switch_angle1 = atan(4.61/inter_axes);

switch_width = 28.2;
switch_height = 16;
switch_deep = 9.70;



module target(angle) {
    
    
}

// hole 1.5 du bord
switch_holes_size = 3;
switch_edge_distance = 1.3;

module switch_holes(d=switch_holes_size, h = 10) {
      // 3mm
        translate([ d/2 + switch_edge_distance,
                    d/2 + switch_edge_distance,
                    0])
        cylinder(d=d,h=h);
        
        translate([switch_width - (d/2 + switch_edge_distance), 
                  switch_height - (d/2 + switch_edge_distance),
                  0])
        cylinder(d=d,h=h);
    
}

module switch_body() {

    difference() {
        translate([ +switch_width/2,
                    switch_height/2,
                    switch_deep/2])
        switch_body_centered()
        //cube(size=[switch_width, switch_height, switch_deep]);
        switch_holes();
    }
}

module switch_body_centered() {
    box(size=[switch_width, switch_height, switch_deep]);
}

module switch(angle = switch_angle0, drawboth=0) {
    
    switch_body();

    // axe
    t_width = 0.6;
    t_large = 4.4;
    h_axe = 2.5;

    inter_axes = 24.45;
    /// boule en bout
    touch_diameter=4.77;
    touch_large = 4.4;

    if (drawboth == 1) {
            
        translate([-t_width/2 + switch_width/2,switch_height - h_axe,switch_deep/2])
        rotate([0,0,90 - switch_angle0])
        box([t_width,inter_axes,t_large], anchor=[0,-1,0])
        align([0,1,0])
        rod(d=touch_diameter, h=touch_large, anchor=[0,0,0]);


        translate([-t_width/2 + switch_width/2,switch_height - h_axe,switch_deep/2])
        rotate([0,0,90 - switch_angle1])
        box([t_width,inter_axes,t_large], anchor=[0,-1,0])
        align([0,1,0])
        rod(d=touch_diameter, h=touch_large, anchor=[0,0,0]);

            
        
        
    } else {
            
        translate([ -t_width/2 + switch_width/2,
                    switch_height - h_axe,
                    switch_deep/2])
        rotate([0,0,90 - angle])
        box([t_width,inter_axes,t_large], anchor=[0,-1,0])
        align([0,1,0])
        rod(d=touch_diameter, h=touch_large, anchor=[0,0,0]);
    }
}

// switch();

// place connexions 

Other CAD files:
doc/3dviews/view_2_modules_with_cut_r.stl
3DModel/28byj-48.scad
3DModel/old_fixtures.scad

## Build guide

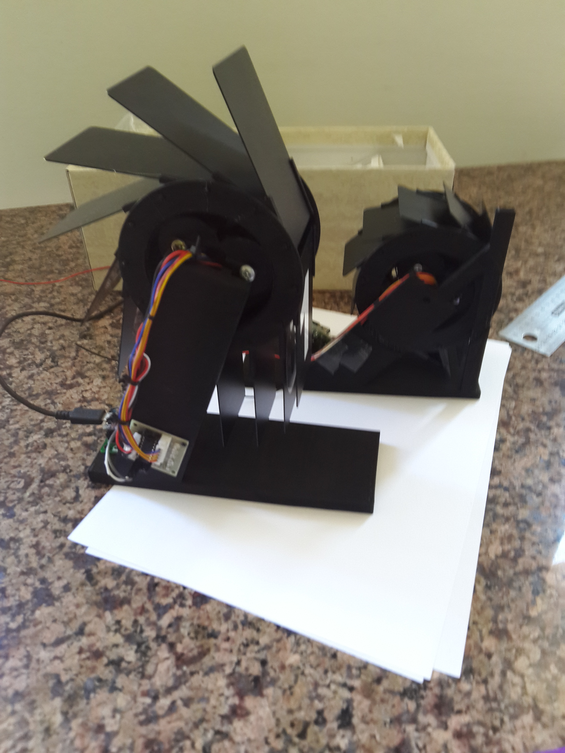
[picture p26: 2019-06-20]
doc/pictures/build/20190616_161145.jpg

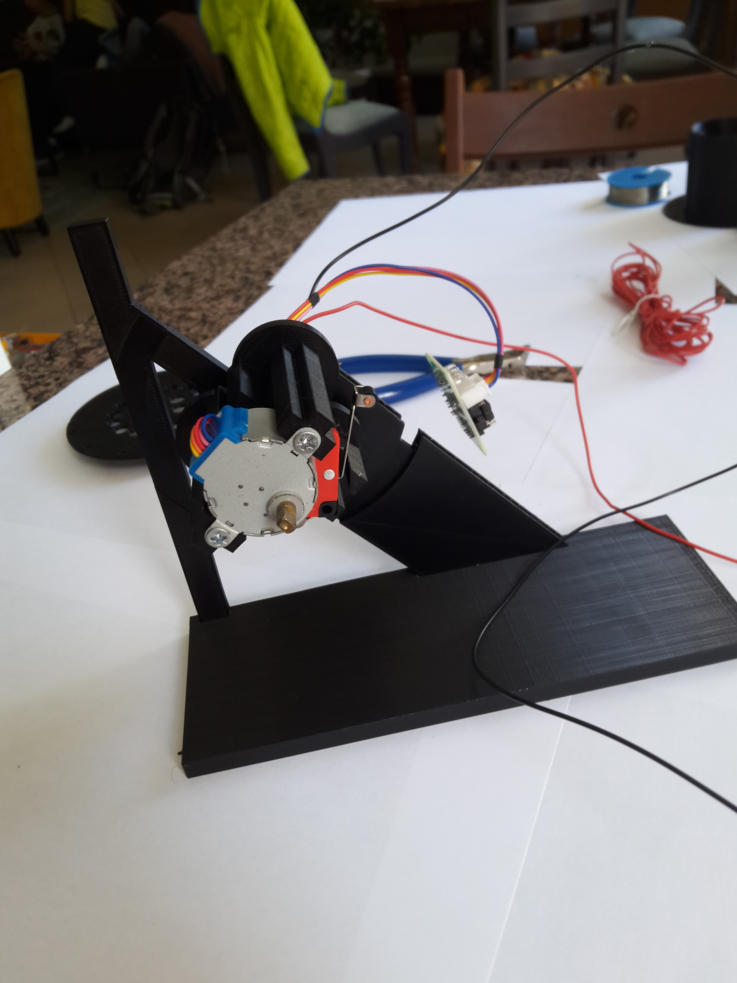
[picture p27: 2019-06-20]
doc/pictures/build/20190616_150015.jpg

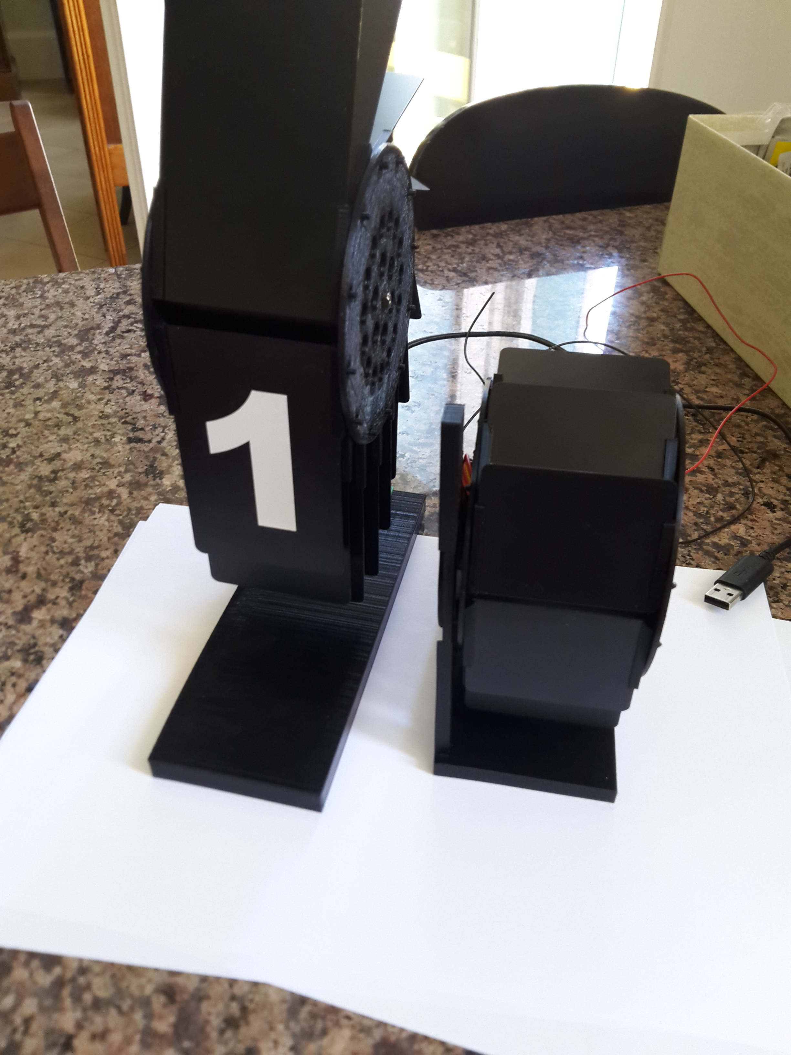
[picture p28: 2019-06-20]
doc/pictures/build/20190616_160147.jpg

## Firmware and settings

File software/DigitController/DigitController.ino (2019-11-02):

// Real Time Kernel
#include <Arduino_FreeRTOS.h>
#include "queue.h"

#include <EEPROM.h>

// Library for controling the stepper
#include "CheapStepper.h"

// manage the parsing of commands
#include "DigitCommandParser.h"

// Number of digits depends on the mecanical design
#define NUMBER_OF_DIGITS 12
#define MESSAGE_MAX_SIZE 30

// Time to wait on the message queue
#define MAXTOWAIT 100

#include <SoftwareSerial.h>



void TaskSerialProtocol(void *parameters);


/* Define the data type that will be queued. */
typedef struct A_Message
{
 char ucData[ MESSAGE_MAX_SIZE ];
} AMessage;

/* Define the queue parameters. */
#define QUEUE_LENGTH 2
#define QUEUE_ITEM_SIZE sizeof( AMessage )


static QueueHandle_t xFrontSendingQueue;
static QueueHandle_t xBackSendingQueue;

// attributed address of the module
static uint8_t attributedAddress = -1;


// global positionning (motor)
static int currentStep = -1;

// total step = -1 -> no homing done yet
static int totalSteps = -1;

// programmable offset
static int offsetStep = 0;

#define EEPROM_OFFSET_STORAGE_ADDRESS 0
#define EEPROM_OFFSET_STORAGE_MAGIX_HEADER 0xCC


  /*
  PIN D8 -> RX
  PIN D9 -> TX
  */
SoftwareSerial ds(8, 9); // RX, TX

int readOffsetValue() {
  byte v1 = EEPROM.read(EEPROM_OFFSET_STORAGE_ADDRESS);
  if (v1 != EEPROM_OFFSET_STORAGE_MAGIX_HEADER) {
    // no magic at start, no value read
    return 0; 
  }

  byte b1 = EEPROM.read(EEPROM_OFFSET_STORAGE_ADDRESS + 1);
  byte b2 = EEPROM.read(EEPROM_OFFSET_STORAGE_ADDRESS + 2);
 
  return b1 + (b2 << 8) - 2^15;
}

void writeOffsetValue(int valueToWrite) {
  uint16_t v = valueToWrite + 2^15;
  byte b1 = v & 0xFF;
  byte b2 = (v >> 8) & 0xFF;
  EEPROM.write(EEPROM_OFFSET_STORAGE_ADDRESS, EEPROM_OFFSET_STORAGE_MAGIX_HEADER);
  EEPROM.write(EEPROM_OFFSET_STORAGE_ADDRESS + 1, b1);
  EEPROM.write(EEPROM_OFFSET_STORAGE_ADDRESS + 2, b2);
}



void setup() {

  offsetStep = readOffsetValue();
  
  // initialize serial communication at 115200 bits per second for main serial
  Serial.begin(115200);
  Serial.print(offsetStep);

  // init back and front serial to 9600 bauds
  Serial1.begin(9600);
  ds.begin(9600);
  
 // while (!Serial) {
    ; // wait for serial port to connect. Needed for native USB, on LEONARDO, MICRO, YUN, and other 32u4 based boards.
 // }
  
   // Create the queue, storing the returned handle in the xQueue variable. 
  xFrontSendingQueue = xQueueCreate( QUEUE_LENGTH, QUEUE_ITEM_SIZE );
  if( xFrontSendingQueue == NULL )
  {
      // The queue could not be created. 
      Serial.println("Front Queue cannot be created");
  }

  // Create the queue, storing the returned handle in the xQueue variable. 
  xBackSendingQueue = xQueueCreate( QUEUE_LENGTH, QUEUE_ITEM_SIZE );
  if( xBackSendingQueue == NULL )
  {
      // The queue could not be created.
      Serial.println("Back Queue cannot be created");
  }

   
    // Now set up two tasks to run independently.
  xTaskCreate(
    TaskMotor
    ,  (const portCHAR *)"Motor Report"   // A name just for humans
    ,  128  // This stack size can be checked & adjusted by reading the Stack Highwater
    ,  NULL
    ,  2  // Priority, with 3 (configMAX_PRIORITIES - 1) being the highest, and 0 being the lowest.
    ,  NULL );

    
  // Now set up two tasks to run independently.
  xTaskCreate(
    TaskSerialProtocol
    ,  (const portCHAR *)"Serial"   // A name just for humans
    ,  300  // This stack size can be checked & adjusted by reading the Stack Highwater
    ,  NULL
    ,  2  // Priority, with 3 (configMAX_PRIORITIES - 1) being the highest, and 0 being the lowest.
    ,  NULL  );

  initMotor();
  
 
  vTaskStartScheduler();
}



static int objectifStep = -1; // no objectives


// Protocol handling
//    0 - Wait for Assigned Number
//    1 - Wait for Commands
//    

boolean startsWith(char *str, char *pattern) {
  unsigned int i = 0;
  for (;;) {
    if (str[i] == 0) {
      if (pattern[i] == 0) {
        // end of both
        return true;
      }
      // end of string
      return false;
    }
    if (pattern[i] == 0) {
      // end of pattern
      return true; 
    }
    if (str[i] != pattern[i]) {
      return false;
    }
    i++;
  }
}


void commandCanceled() {
  Serial.println("commandCanceled");
}

int readUpStream() {
  return Serial1.read();
}

int readUpStream2() {
  return Serial.read();
}


int readDownStream() {
  return ds.read();
}


static AMessage bufferMessage;
void pushMessageToQueue(char* message,QueueHandle_t queue) {

  int message_length = strlen(message);
  // copy message
  sprintf(bufferMessage.ucData, "S%03d%s\n", message_length, message);
  if (xQueueSend(queue, &bufferMessage, MAXTOWAIT) != pdPASS) {
    // issue in posting the element on the queue
    Serial.println(F("error in pushing the message"));
  }  
}

void moveTo(uint16_t digit) {
  uint16_t stepsInterval = totalSteps / NUMBER_OF_DIGITS;
  uint16_t s =  (digit * totalSteps / NUMBER_OF_DIGITS + stepsInterval * 3 / 4 + offsetStep) % totalSteps;
  objectifStep = s;
}

void processBackCommand(const char *command) {
  Serial.print(F("Command from Back Executed :"));
  Serial.println(command);

  // push command to front
  pushMessageToQueue(command, xFrontSendingQueue);  
}

void processFrontCommand(const char *command) {
  
  Serial.print(F("Command from Front Executed :"));
  Serial.println(command);
  char message[MESSAGE_MAX_SIZE];

  if (startsWith(command,"MOVE-")) { // use char * to avoid String usage
    
    int steps = atoi((char *)(command + 5));
    objectifStep = steps;
    // Serial.println(objectifStep);
    
  } else if (startsWith(command, "HELLO")) {
    
    // respond
    pushMessageToQueue("HELLO", xFrontSendingQueue);
    
  } else if (startsWith(command, "IAM-")) {
    
    // Receive the number from 
    int frontAddress = atoi((char *)(command + 4));
    attributedAddress = frontAddress + 1;
    // send the same message to the other following ones
    sprintf(message, "IAM-%d",attributedAddress);
    pushMessageToQueue(message, xBackSendingQueue );
    
  } else if (startsWith(command, "OFFSET-")) { 
    // define the offset of the digit (from the homing button)
    int offset = atoi((char *)(command + 7));
    offsetStep = offset;
    writeOffsetValue(offset);
    Serial.println(offsetStep);
  
  } else if (startsWith(command, "DIGIT-")) {
    // command to directly send a digit display
    uint16_t digit =atoi((char *)(command + 6));
    moveTo(digit);
    
  } else if (startsWith(command, "DISPLAY-")) {
     // from the current address position, 
     // grab the display character and apply it

     // forward the message to back
     pushMessageToQueue(command, xBackSendingQueue);

     // handle it's owwn digit
     // char index
     uint8_t offset = 8 + attributedAddress;
     if (offset >= 8) {
       // Serial.println(command[offset]);
       uint16_t digit = command[offset] - '0';
       moveTo(digit);
     }

     sprintf(message, "ACKDISPLAY-%d", attributedAddress);
     
     // send ACK
     pushMessageToQueue(message, xFrontSendingQueue);
     
  } 
  else if (startsWith(command, "CMD-")) {
      // format of the message is
      //XXXCMD-NNN-XXXHELLO
      char read_address[5];
      strncpy(read_address, (char *)(command + 4), 3);
      read_address[3] = '\n';
      uint16_t address = atoi(read_address);
      char * inner_command_pointer = (char *)(command + 4 + 3 /* digits number for inner command */ + 1 /* separator */);
      if (address == attributedAddress) {
        // this command is for this module, 
        // handle it
        processFrontCommand(inner_command_pointer);
      } else {
        // forward to back
        pushMessageToQueue(inner_command_pointer, xBackSendingQueue );
      }
      
  }
  else 
  {
    Serial.println(F("unknown command"));
  }
  
}

// structure used for front parsing
static parser_t frontParser;

// structure used for front parsing2
static parser_t frontParser2;

// structure used for back message parsing
static parser_t backParser;

// Working message
static AMessage m;

// Serial State automaton
// and Serial sending
void TaskSerialProtocol(void *parameters) {
   
    init(&frontParser);
    init(&frontParser2);
    init(&backParser);
  
    for(;;) {

       // receive from usb
       while(handleSerialReceive(&frontParser2, &processFrontCommand, &readUpStream, &commandCanceled) > 0){};
       
       // receive front
       while (handleSerialReceive(&frontParser, &processFrontCommand, &readUpStream2, &commandCanceled) > 0) {};

       // receive back
       while (handleSerialReceive(&backParser, &processBackCommand, &readDownStream, &commandCanceled) > 0) {};

       // send front messages
        if (uxQueueMessagesWaiting( xFrontSendingQueue ) > 0) {
             if (xQueueReceive(xFrontSendingQueue, &m, ( TickType_t ) 0) == pdPASS) {
             // send message to front
             Serial.print(F("front send message:"));
             Serial.println(m.ucData); // usb connection
             Serial1.println(m.ucData); // and front
           }
        }
       
       // send back messages
      if (uxQueueMessagesWaiting( xBackSendingQueue ) > 0) {
             if (xQueueReceive(xBackSendingQueue, &m, ( TickType_t ) 0) == pdPASS) {
             // send message to back
             Serial.print(F("back send message:"));
             Serial.print(m.ucData);
             ds.println(m.ucData);
           }
        }

       vTaskDelay(1);
       
    }
}


////////////////////////////////////////////////////////////////
// Motor Controlling
// 
//  Motor is handled on interrupts to avoid the 15ms watch dog timer of 
//  FreeRT Os
//  This also smooth the move

// Pins in the design
const int IN1 = 10;
const int IN2 = 16;
const int IN3 = 14;
const int IN4 = 15;

// Homing SWITCH READING
const int SWITCH = 18;

// managing the stepper steps
static const CheapStepper cs = CheapStepper(IN1,IN2,IN3,IN4);

void initMotor() {
  
    // Motor interrupt handling

    pinMode(IN1,OUTPUT);
    pinMode(IN2,OUTPUT);
    pinMode(IN3,OUTPUT);
    pinMode(IN4,OUTPUT);
  
    pinMode(SWITCH,INPUT);

    DDRC |= 0x80;
    cli();          // disable global interrupts
    TCCR1A = 0;     // set entire TCCR1A register to 0
    TCCR1B = 0;     // same for TCCR1B
    // set compare match register to desired timer count
    // 13 -> too fast for BYMOTORS
    OCR1A = 20;
    // turn on CTC mode:
    TCCR1B |= (1 << WGM12);
    // Set CS10 and CS12 bits for 1024 prescaler
    TCCR1B |= (1 << CS10);
    TCCR1B |= (1 << CS12);
    
    // enable timer compare interrupt
    TIMSK1 |= (1 << OCIE1A);
    // enable global interrupts
    
    sei();
}


static bool isIn = false;
static int nbIn = 0;


const int T_THRESHOLD = 100;

ISR(TIMER1_COMPA_vect) {

    // totalSteps < 4060 means the homing
    // has not been done yet
    
    if (totalSteps < 4060 || 
          (objectifStep != currentStep && objectifStep > 0) ) {
    
          cs.move(true,1);
          if (currentStep >=0) {
            currentStep ++;
              if (currentStep == objectifStep) {
                cs.stopCurrent();
              }
          }

            // watch the homing state
        
            int value = analogRead(SWITCH);
            
            // measure threshold
            if (value > 10) {
              // floating value
               if (!isIn) {
                  nbIn ++;
                  nbIn = nbIn > T_THRESHOLD ? T_THRESHOLD : nbIn;
               }
            } else {
              nbIn--;
              nbIn = nbIn <= 0 ? 0 : nbIn - 1; 
            }
        
            if (nbIn >= T_THRESHOLD) {
              isIn = true;
            }
        
            if (nbIn <= 0 && isIn) {
              // homing point
              if (currentStep < 0) {
                currentStep = 0;
              } else {
                // adjust the stepnumber
                bool inHoming = (totalSteps == -1);
                totalSteps = currentStep;
                currentStep = 0;
                if (inHoming) {
                  // next first objective is 0
                  moveTo(0);
                }
              }
               isIn = false;
            } 
    } // if (homing or target)
}

void TaskMotor(void *parameters) {
  
  Serial.println(F("Motor initialized"));
  for(;;) {
      vTaskDelay(100);
      char buffer[20];
      sprintf(buffer, "%d / %d", currentStep, totalSteps);
      Serial.println(buffer);
  }
}

void loop() {
  //nothing to do, tasks are running
}

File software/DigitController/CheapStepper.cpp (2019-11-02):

/*  CheapStepper.cpp - 
	v0.2
	Library for the 28BYJ-48 stepper motor, using ULN2003 driver board
	https://arduino-info.wikispaces.com/SmallSteppers

	Library written by Tyler Henry, 6/2016

	uses 8-step sequence: A-AB-B-BC-C-CD-D-DA

	motor has gear ratio of either:
		64:1 (per manufacturer specs)
		or 
		63.68395:1 measured
			(see: http://forum.arduino.cc/index.php?topic=71964.15)
	* 64 steps per internal motor rev
	= 

	4096 total mini-steps / revolution
	or ~4076 (4075.7728) depending on exact gear ratio

	assumes 5v power source for rpm calc
*/


#include "Arduino.h"
#include "CheapStepper.h"


CheapStepper::CheapStepper () {
	for (int pin=0; pin<4; pin++){
		pinMode(pins[pin], OUTPUT);
	}
}

CheapStepper::CheapStepper (int in1, int in2, int in3, int in4) {

	pins[0] = in1;
	pins[1] = in2;
	pins[2] = in3;
	pins[3] = in4;
	CheapStepper();
}


void CheapStepper::move (bool clockwise, int numSteps){

	for (int n=0; n<numSteps; n++){
		step(clockwise);
	}
}


void CheapStepper::step(bool clockwise){

	if (clockwise) seqCW();
	else seqCCW();
}

void CheapStepper::stopCurrent() {
  seq(8);
}


/////////////
// PRIVATE //
/////////////



void CheapStepper::seqCW (){
	seqN++;
	if (seqN > 7) seqN = 0; // roll over to A seq
	seq(seqN);

	stepN++; // track miniSteps
	if (stepN >= totalSteps){
		stepN -=totalSteps; // keep stepN within 0-(totalSteps-1)
	}
}

void CheapStepper::seqCCW (){
	seqN--;
	if (seqN < 0) seqN = 7; // roll over to DA seq
	seq(seqN);

	stepN--; // track miniSteps
	if (stepN < 0){
		stepN +=totalSteps; // keep stepN within 0-(totalSteps-1)
	}
}

void CheapStepper::seq (int seqNum){

	int pattern[4];
	// A,B,C,D HIGH/LOW pattern to write to driver board
	
	switch(seqNum){
		case 0:
		{
			pattern[0] = 1;
			pattern[1] = 0;
			pattern[2] = 0;
			pattern[3] = 0;
			break;
		}
		case 1:
		{
			pattern[0] = 1;
			pattern[1] = 1;
			pattern[2] = 0;
			pattern[3] = 0;
			break;
		}
		case 2:
		{
			pattern[0] = 0;
			pattern[1] = 1;
			pattern[2] = 0;
			pattern[3] = 0;
			break;
		}
		case 3:
		{
			pattern[0] = 0;
			pattern[1] = 1;
			pattern[2] = 1;
			pattern[3] = 0;
			break;
		}	
		case 4:
		{
			pattern[0] = 0;
			pattern[1] = 0;
			pattern[2] = 1;
			pattern[3] = 0;
			break;
		}
		case 5:
		{
			pattern[0] = 0;
			pattern[1] = 0;
			pattern[2] = 1;
			pattern[3] = 1;
			break;
		}
		case 6:
		{
			pattern[0] = 0;
			pattern[1] = 0;
			pattern[2] = 0;
			pattern[3] = 1;
			break;
		}
		case 7:
		{
			pattern[0] = 1;
			pattern[1] = 0;
			pattern[2] = 0;
			pattern[3] = 1;
			break;
		}
		default:
		{
			pattern[0] = 0;
			pattern[1] = 0;
			pattern[2] = 0;
			pattern[3] = 0;
			break;
		}
	}

	// write pattern to pins
	for (int p=0; p<4; p++){
		digitalWrite(pins[p], pattern[p]);
	}
}

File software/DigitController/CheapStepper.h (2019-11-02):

/*  CheapStepper.h - 
	v0.2
	Library for the 28BYJ-48 stepper motor, using ULN2003 driver board
	https://arduino-info.wikispaces.com/SmallSteppers

	Library written by Tyler Henry, 6/2016

	uses 8-step sequence: A-AB-B-BC-C-CD-D-DA

	motor has gear ratio of either:
		64:1 (per manufacturer specs)
		or 
		63.68395:1 measured
			(see: http://forum.arduino.cc/index.php?topic=71964.15)
	* 64 steps per internal motor rev
	= 

	4096 total mini-steps / revolution
	or ~4076 (4075.7728) depending on exact gear ratio

	assumes 5v power source for rpm calc
*/

#ifndef CHEAPSTEPPER_H
#define CHEAPSTEPPER_H

#include "Arduino.h"

class CheapStepper
{

public: 
	CheapStepper();
	CheapStepper (int in1, int in2, int in3, int in4);

	void set4076StepMode() { totalSteps = 4076; }
 
	void setTotalSteps (int numSteps) { totalSteps = numSteps; }
	// allows custom # of steps (usually 4076)

	// blocking! (pauses arduino until move is done)
	void move (bool clockwise, int numSteps); // 4096 steps = 1 revolution


	// non-blocking versions of move()
	// call run() in loop to keep moving


	void step (bool clockwise);
	// move 1 step clockwise or counter-clockwise

	void stepCW () { step (true); } // move 1 step clockwise
	void stepCCW () { step (false); } // move 1 step counter-clockwise

	int getStep() { return stepN; } // returns current miniStep position
	int getPin(int p) { 
		if (p<4) return pins[p]; // returns pin #
		return 0; // default 0
	}
	int getStepsLeft() { return stepsLeft; } // returns steps left in current move

  void stopCurrent();

private:


	void seqCW();
	void seqCCW();
	void seq(int seqNum); // send specific sequence num to driver

	int pins[4] = {8,9,10,11}; // in1, in2, in3, in4

	int stepN = 0; // keeps track of step position
	// 0-4095 (4096 mini-steps / revolution) or maybe 4076...
	int totalSteps = 4096;

	int seqN = -1; // keeps track of sequence number

	// variables for non-blocking moves:
	unsigned long lastStepTime; // time in microseconds that last step happened
	int stepsLeft = 0; // steps left to move, neg for counter-clockwise

};

#endif

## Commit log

2019-04-22 initial import after a first prototype
    [28byj-48.scad, digit_flip.scad]
2019-04-28 update after several tests
    [electronic.fzz, electronic_2.fzz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]
2019-04-28 update main design
    [digit_flip.scad]
2019-04-28 update documentation
    [electronic_2.fzz]
2019-04-28 add video for showing deport effect
    [electronic_2.fzz]
2019-05-13 add microswitch
    [digit_flip.scad, switch.scad]
2019-05-14 add ramp for avoid supports
    [digit_flip.scad]
2019-05-26 remove pde, update schema to switch
    [digit_flip.scad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]
2019-06-01 wip, motor control implemented
    [2019-04-27_electronic.fzz, digit_flip.scad]
2019-06-01 update width, for play
    [digit_flip.scad]
2019-06-02 add 1st support design
    [28byj-48.scad, digit_flip.scad, support.scad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]
2019-06-07 update software
    [support.scad]
2019-06-09 update 3D model
    [digit_flip.scad, old_fixtures.scad, support.scad]
2019-06-09 improve 3D Model
    [digit_flip.scad, support.scad]
2019-06-15 improve doc, add exploded vision, update readme
    [digit_flip.scad, support.scad]
2019-06-16 refactor fixture
    [digit_flip.scad]
2019-06-20 add play on rotor
    [digit_flip.scad]
2019-06-20 improve documentation
    [support.scad]
2019-06-25 add doc, debug print the steps, change dalle
    [digit_flip.scad, support.scad]
2019-06-30 add test for serial in / out
    [digit_flip.scad, support.scad]
2019-09-04 work in progress
    [digit_flip.scad, electronic_v3.fzz]
2019-09-04 move electronic design to electronic, improve documentation
    [electronic_2.fzz, electronic_v3.fzz, electronic_v4.fzz]
2019-09-04 add sample artwork for cards
2019-09-08 fix V4 electronic card, add chain control
    [electronic_v4.fzz]
2019-09-29 add doc, media
    [axe.stl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]
